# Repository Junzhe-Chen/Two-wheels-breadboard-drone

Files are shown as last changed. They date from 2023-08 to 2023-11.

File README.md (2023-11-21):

# Overview

The two wheel car is built onto a small breadboard, with an Arduino Uno attached at the bottom. There are two small DC motor which acts as the driver of the motor each with a dedicate full H bridge to control it. The robot also contains an ultrasonic sensor that is used to avoid obstacles. 

# Basic structure

The drone looks like this:

Overview of the drone

The drone is composed of 4 parts:

- 9V battery as the power source

9V battery power

- Arduino Uno R3 for the control

Arduino UNO

- Breadboard for attaching electrical components

Breadboard

- motors that makes the robot move

Motor

I tried to print out the wheel on a 3D printer, then I screwed up… **Bruh**

Failed 3D printing residue

If the wheel is designed to be 3D printed out, one thing to keep notice that is the wheel should have abundance contact with the plate of the 3D printer, which ensures the print stays in its place while printing. My first print has relatively thin structure (to save material) which does not provide enough contact area to the plate, causing the print to fail eventually. 

In my second design, I make the wheel more beefy and so far the print is going OK.

One of the objective of the project is to make the robot 

- able to move forward, backward, left and right
- can avoid obstacle (if there is a obstacle in the front of the robot, it should be able to go around and pass it)
- having the lighting in the front which can be turned on and off by the Arduino

## Movement control

### Little catch, Does the motor really work?

I have tested the motor with quite optimistic mindset for a bit, and found out it cannot drive the drone rather easily.

While the motor can perform well in empty load, it does not drive the wheel (which is around 20g of PLA print) that well. One reason is the small motor I used in this project is not designed to have great torque to drive heavy load. According to the datasheet shown below, it drives approximately 10g-cm torque, which is definitely a small value for driving the drone which have the total weight around 500g.

motor's datasheet

While if I can use a continuous servo motor, the torque it can provide is much more greater, which can potentially provide better drivability for this project. A typical SG90 microservo can provide around 2.5kg-cm torque, which is **much** bigger (250 times) than the motor that is mentioned previously. The datasheet for the SG90 servo motor is shown below;
microservo's datasheet

The microservo achieves that by applying gearbox inside the structure which by using small gear ratio, to increase the torque while reduce the speed. In this specific application, we don't need extremely fast spin of the motor (we are not making a fan or a propeller anyway), but we need generaous amount of torque to drive it forward. That is one reason why I decided to change the motor into microservo (which also saves plenty of breadboard space from the H bridge that is mentioned above).

### Working principle of the microservo

There are two types of microservo, one is those you can control the angle it turns between e.g. 0 and $180^\circ$, which is often used in the scenario where precision is the key. One good example of this type of microservo is [SG90](https://www.amazon.co.uk/s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)

However, in this project, the key is to make the wheel moving constantly. In this case, we should consider using a continuous microservo. The working mechanism of those servo motor is when you give a short pulse duration (for example, 0.5ms), it will rotate in one direction; When you apply a longer pulse (for example, 1.5ms), it will rotate in the opposite direction. This satisfies the bare minimum requirements for making a movement control for a two wheel drone, as it should be sufficient with forward and backward motion with controllable speed. A typical continuous servomotor is [FS90R](https://www.rapidonline.com/Feetech-FS90R-360-Continuous-Rotation-Micro-Servo-37-1335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)

in the Arduino library, we can include the servo header file, which provide the way to control most servo on the market. In my case, I am using the FS90R continuous microservo for my drone's movement. By using the header file, if I do `servo.write(90);` to my servo, it will stop and stay at neutral position. If I make the value smaller, it will constantly spin at one direction and same thing happen if I make the value bigger than 90, but the direction will be inverted. 

However, please take note that when we mount the motor to the breadboard, the two motor will be mirror to each other. Which means if both microservo have the same input (for example, `leftServo.write(80);` and `rightServo.write(80);` as the servo input), it will not go straight, but make the drone spin. In order to make the drone move forward, it should write the following:

```c++
void forward() {
  leftServo.write(90 - FORWARD_SPEED);
  rightServo.write(90 + FORWARD_SPEED);
}
```

But if I want the drone to spin around, I should write give the microservo the same input, like what is shown below:
```c++
void spin_left() {
  leftServo.write(90 - FORWARD_SPEED);
  rightServo.write(90 - FORWARD_SPEED);
}
```

## Choosing the battery

Interestingly, choosing the suitable battery for this project is the most time-consuming thing for me. The challenge in this part is to find a battery that can supply high current without too much voltage drop. The following picture shows that when the wheel is changing the direction, it will require high current up to around 0.8A to 1A. 

Current

One interesting thing is when the battery is drawing too much current, the battery voltage will decrease a lot. The unfortunate truth is if the supply voltage run below 4V for the Arduino, the Arduino will turn off, therefore the program will not run. 

Initially, I used the 1604S 9V battery as it marked “super heavy duty”, but it turned out not as that “heavy duty”. When driving the battery with 1A of current, the voltage quickly dropped down below 1V. After reviewing the [datasheet](https://www.farnell.com/datasheets/612533.pdf) for that battery, it shows that the main focus for the battery is longevity, as it will last quite a long time compare with other 9V battery. The battery that I chose for my project is 1604A (the golden one shown below) which has better current drivability and it is designed to handle high current. 

Batteries

As it said in the introduction page at [Farnell](https://uk.farnell.com/gp-batteries/gp1604-10/battery-alkaline-pp3-pk10/dp/5057050):

> High power, long-life alkaline PP3 batteries giving up to six times the life of ordinary zinc carbon batteries; ideal for high drain applications
> 

which turned out to be good enough for this project.

## Obstacle avoiding logic

In order to make the robot avoid obstacle, we need some sort of sensor that can be used to detect the distance between the robot and the surrounding. For this specific use case, the following sensor can be chosen:

- Ultrasonic sensor
    - Relatively cheap and easy-to-use, limited range (till around 0.5m), limited speed, take extra caution about the glitch when the sensor is too close to the wall
- IR sensor
    - Great accuracy and speed, limited range (depending to the ambient light) and light dependant, not that great for this use case
- LiDAR
    - [GreatScott!! video](https://youtu.be/_--8K1BW_O4)
    - adaptive scanning (sounds cool)

In this documentation, I will focus on the ultrasonic sensor one, because the sensor is readily available in my university lab and I had past experience with that. In the future, I might consider using LiDAR and according to GreatScott, it is definitely doable and it can give much more accurate control (just look at the commercial sweeping robot, they use LiDAR to avoid obstacle, meanwhile, map the room)

### Basics of ultrasonic sensor

As we all know, sound travels around $340m/s$ in the air. Remember this data, which will be quite useful in the future.

[insert image for better explanation]

 The principle of the ultrasonic sensor is to send a short pulse in certain time period, and receive the same pulse with the receiver. By calculating the time difference between sending and receiving signal, the distance can be calculated by the following equations:

$$
d=\frac{340}{2t}
$$

where $d$ represents the distance between the sensor and the obstacle, $t$ is the time between the pulse being sent and the time where signal being received.

By using this principle, we can write following codes in Arduino to sense the distance between the sensor and the obstacle.

```c++
void distance_measurement() {
    if (millis() > currentMillis + 100) {  // Distance measurement in every 100 milliseconds
      	currentMillis = millis();

	// generate 10-microsecond pulse to TRIG pin
      	digitalWrite(ULTRASONIC_TRIGGER_PIN, HIGH);
      	delayMicroseconds(10); 
      	digitalWrite(ULTRASONIC_TRIGGER_PIN, LOW);

      	// measure duration of pulse from ECHO pin
      	duration_us = pulseIn(ULTRASONIC_ECHO_PIN, HIGH);

      	// calculate the distance
      	distance_cm = 0.017 * duration_us; // Formular that is mentioned before
      	Serial.println("distance: ");
      	Serial.print(distance_cm);
      	// return distance_cm;
      	// print the value to Serial Monitor
    }
  }
```

According to my test, the ultrasonic sensor's readout is quite accurate. However, it does have some artifacts when the distance between the obstacle and the ultrasonic sensor is too close, which is why I put it around 2 or 3 centimeters inside of the drone to avoid the artifacts happens. The range of the ultrasonic sensor is from 2cm to 1 metre.
ultrasonic measurement

### Detailed look of obstacle avoidance logic with codes

To avoid the obstacle, we need to know few things:

- What is the threshold distance between the robot and the obstacle when you want the robot to avoid the obstacle?
- How does the robot determine whether it should turn left or turn right when facing an obstacle?

Which they sounds easy, but is actually a little tricky to implement when considering the limited space this design has.

As we all know for the ultrasonic sensor (which is the sensor chosen for this project), it only returns the distance in the front, but not the distance around the robot. In order to make the robot know the distance on the left and right side of the robot, there are the following few suggestions:

- Adding two more ultrasonic sensor, one on the left and another on the right. you will only have the gut of doing that if you have unlimited funds (Obviously, I am not), as well as plenty of space for the robot, which is not achievable on a small design like this.
- Mounting the ultrasonic sensor on a servo, making the sensor turn around to check the distance on the left and right hand side of the robot. It works quite like a sweeping radar, which can be quite interesting to make one one day. Unfortunately, there is not enough space for my project to implement this design.
- Rotating the robot to the left and the right to “peek” the distance. This solution is quite bad as it makes the robot constantly turning around. But due to the limited space for adding more components, this is the only way I can use.
- Surely there are more solutions other than that, maybe you can come up with better solution than me!

The flow chart for my version of obstacle avoidance logic is shown below:

Flow chart

where if the sensor returns the distance value less than the threshold, the robot will first move backward to avoid collision, then checking the left and right distance between the robot and the obstacle, so that it can find the easiest path for it to pass through.

Obstacle avoidance illustration

As for the left and right peek, the flow chart and the code is shown below:

flowchart int checkLeft

```cpp
int checkLeft() {
  STOP();
  delay(10);
  spin_left();
  delay(200);  // Calibrate this value till when doing one spin, the robot turns to 45 degrees
  distance_measurement();
  spin_right();
  delay(200); // Spin the robot back after checking left distance
  STOP();
  Serial.print(" >>> Distance to the left is: ");
  Serial.print(distance_cm);
  Serial.println("cm <<<");
  return distance_cm;
}
```

Same thing apply when checking the right side, the only difference will be that the `spin_left()` and `spin_right()` function will be inverted.

## Final demo

Here is a short video footage that shows how the obstacle avoidance function works

https://github.com/Junzhe-Chen/Two-wheels-breadboard-drone/assets/141964509/749089a3-922f-4cfe-97b0-32ad5c9f485c

The **circuit diagram** of the breadboard is shown below, I use [TinkerCAD](www.tinkercad.com) to create it.

![Breadboard diagram]
)

## Few notices and common mistakes

**Please check the following if your robot does not work, it might save you a day!**

1. The battery ground should share with the Arduino ground, if there are not sharing the same ground, the Arduino will be put in the floating state, therefore the voltage reference will not be accurate
2. Careful with your connection of the switch, the left and middle pin should connect to the positive Vin of the Arduino and the positive wire (red wire of the PP3) of the 9V battery. The negative input of the Arduino should not be connected to the switch. If the negative input is connected, when the switch is closed, it will **short** out the Arduino **which will make your unable to download, even worse, destroy your Arduino!**
3. When connecting the cable to the Arduino pin socket, make sure to make the sharp bend. This ensures good connection to the Arduino. You might encounter the robot behaves weirdly and ultrasonic sensor is constantly reading zero, this is usually caused by loose connection between Arduino and ultrasonic sensor
4. You may need to calibrate the microservo more or less. If the microservo does not stop given `servo.Write(90)`, spin the potentiometer at the back of the servo until its stops. Also, the speed of the left and right servo should be calibrated to the same, that makes the robot traveling straight when moving forward

## Bill of Materials:

The Bill of Materials (BoM) of this project is shown below:

If more knockoff brands are used, the cost should be within £40

I might consider making this into a kit in the future according to the requests.

| Component name | Component model  | Quantity | Price per unit | Price Total | Link  (Farnell) |
|---|---|---|---|---|---|
| Breadboard | | 1 | £2.60 | £2.60 | https://uk.farnell.com/multicomp/mcbb400/breadboard-solderless-300v-abs/dp/2395961 |
| Arduino | Arduino UNO R3 | 1 | £10 | £10.00 | Check price on ebay |
| Battery | 9V PP3 battery | 1 | £6 | £6.00 | https://uk.farnell.com/gp-batteries/gppva9vau073/battery-alkaline-pp3-9v/dp/3775309?st=9v%20batteries |
| Continuous servo  | FS90R | 2 | £9 | £18.00 | https://kitronik.co.uk/products/2589-fs90r-360-degree-continuous-rotation-servo |
| Ultrasonic sensor | | 1 | £3 | £3.00 | https://www.ebay.co.uk/itm/155434881025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 |
| Photoresistor | | 1 | | £0.00 | |
| Switch | Any spare switch | 1 | | £0.00 | |
| | | | Subtotal: | £39.60 |

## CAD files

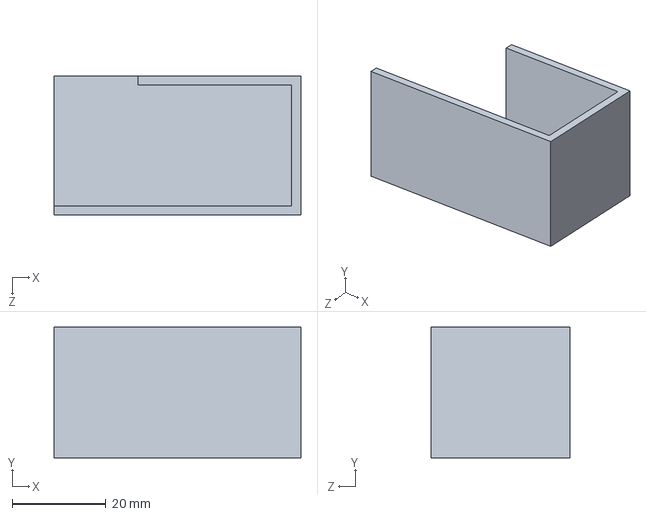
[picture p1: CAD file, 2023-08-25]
3D model, SLDPRT files/Battery holder.SLDPRT
52.8 x 28.0 x 29.8 mm

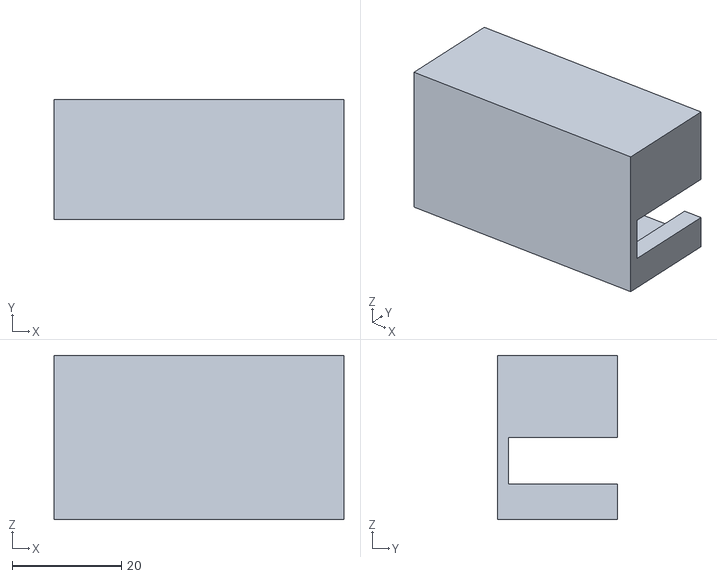
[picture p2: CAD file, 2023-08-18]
Breadboard drone 3D files/Battery holder V1.1.STL
53.0 x 22.0 x 30.0

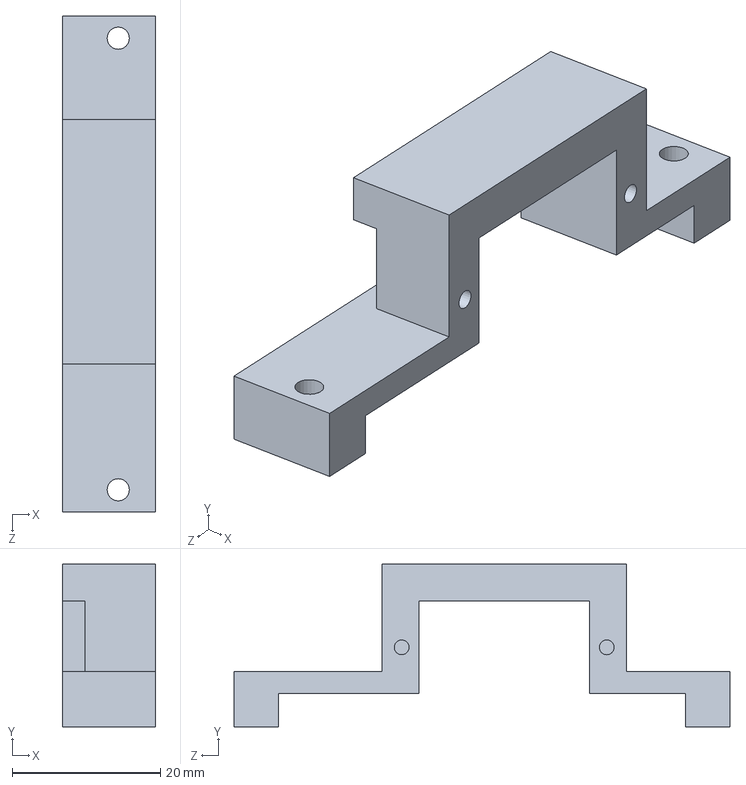
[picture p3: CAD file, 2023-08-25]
3D model, SLDPRT files/Right servo lock.SLDPRT
12.5 x 22.0 x 67.0 mm

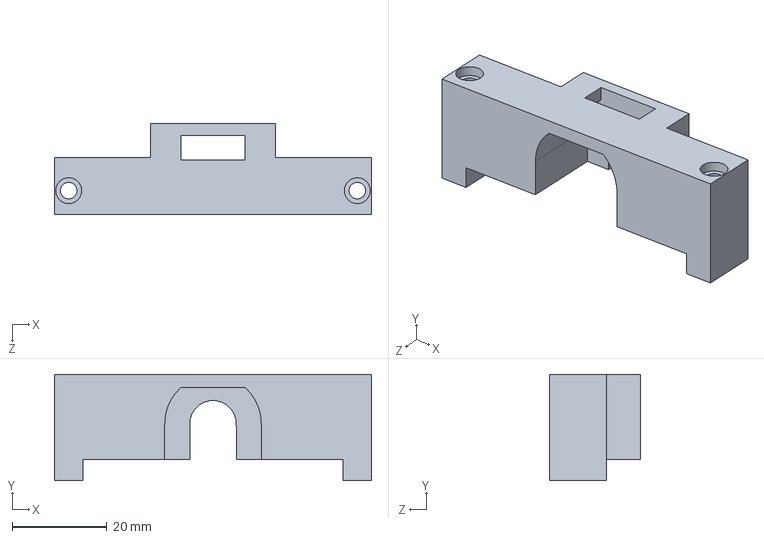
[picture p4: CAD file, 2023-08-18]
Breadboard drone 3D files/DC motor lock V2.3 straight sink.SLDPRT
67.0 x 22.5 x 19.1 mm

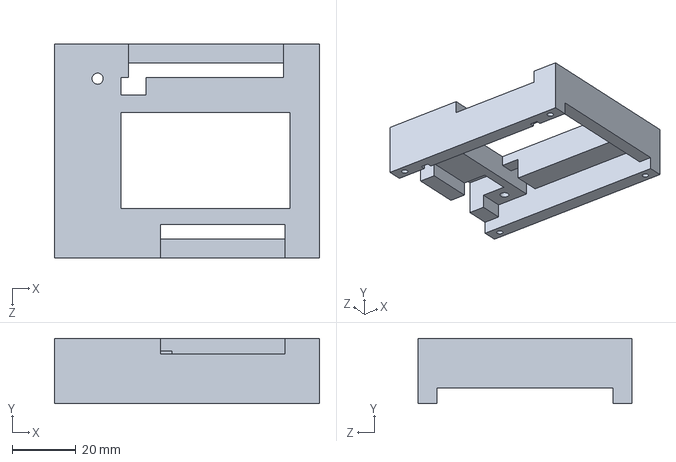
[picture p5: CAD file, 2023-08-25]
3D model, SLDPRT files/Arduino cover.SLDPRT
83.0 x 20.5 x 67.0 mm

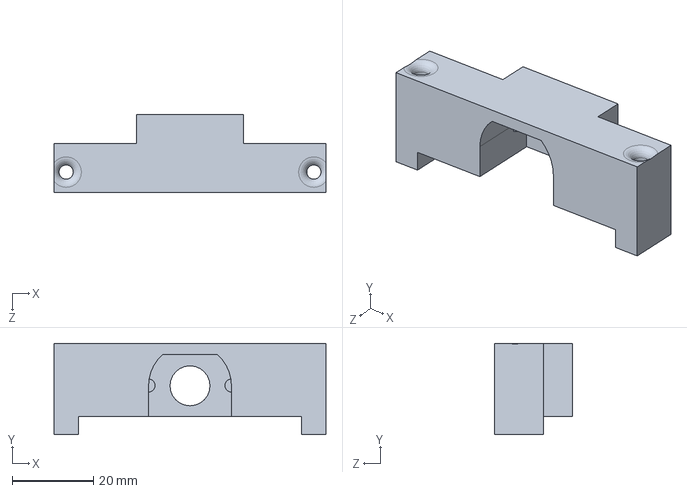
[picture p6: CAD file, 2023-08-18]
Breadboard drone 3D files/DC motor lock V2.2.SLDPRT
67.0 x 22.5 x 19.1 mm

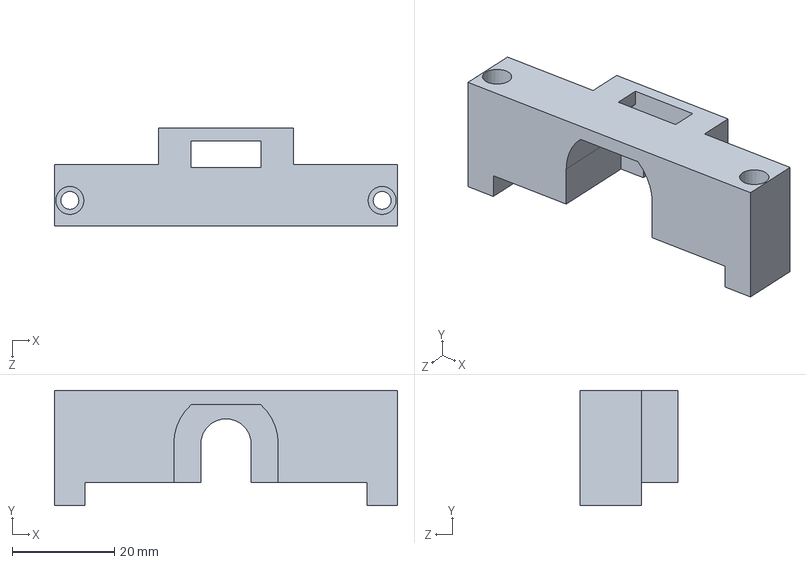
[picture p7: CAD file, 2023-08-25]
3D model, SLDPRT files/DC motor lock.SLDPRT
67.0 x 22.5 x 19.1 mm

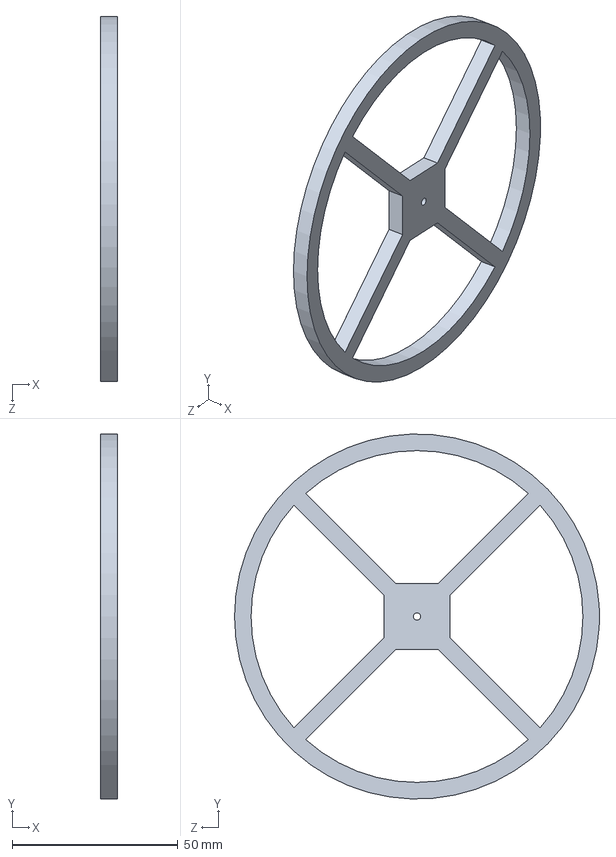
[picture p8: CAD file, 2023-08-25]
3D model, SLDPRT files/Wheel with Servo Cross mount.SLDPRT
5.00 x 110.0 x 110.0 mm

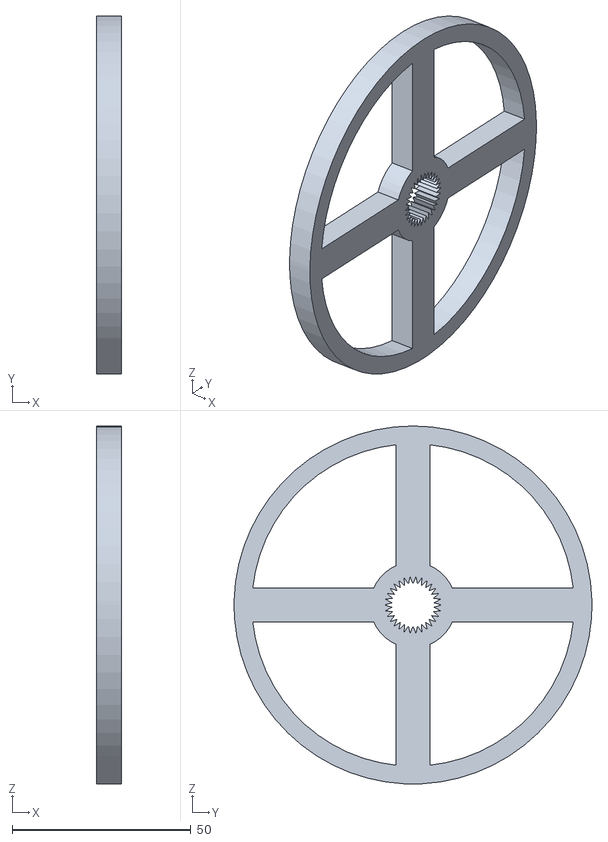
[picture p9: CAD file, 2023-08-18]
Breadboard drone 3D files/Wheel V1.2 test.STL
7.00 x 100.0 x 100.0

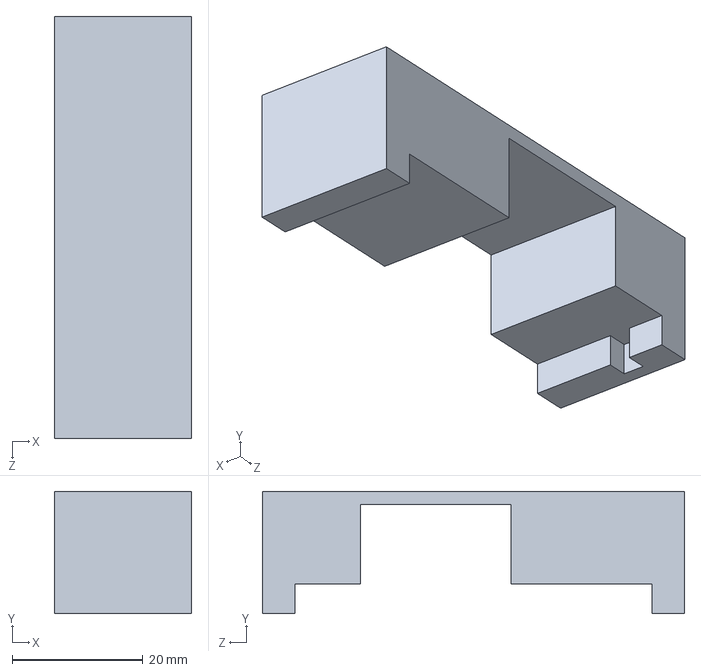
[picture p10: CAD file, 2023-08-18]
Breadboard drone 3D files/Servo lock V1.1.SLDPRT
21.0 x 18.7 x 64.5 mm

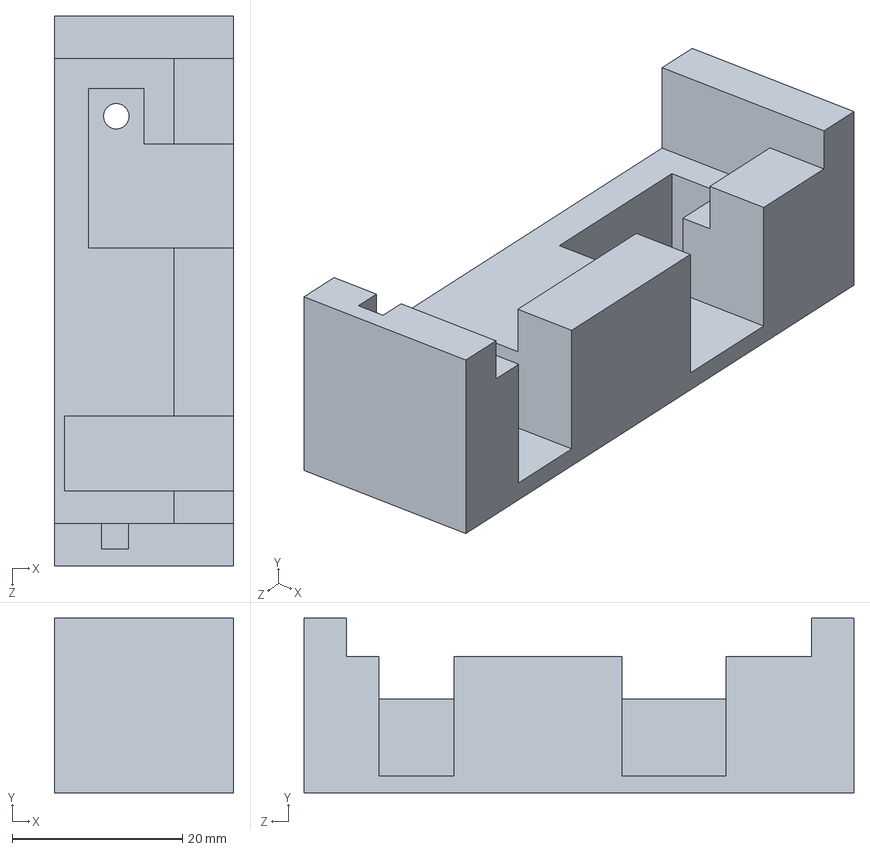
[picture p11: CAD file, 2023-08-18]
Breadboard drone 3D files/Robot base cover V1.2.SLDPRT
21.0 x 20.5 x 64.5 mm

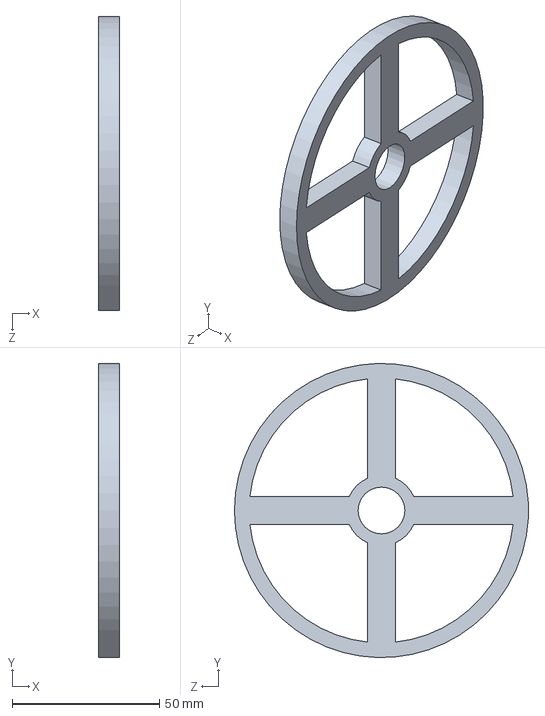
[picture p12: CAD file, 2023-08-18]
Breadboard drone 3D files/Wheel V1.2 no tooth test.SLDPRT
7.00 x 100.0 x 100.0 mm

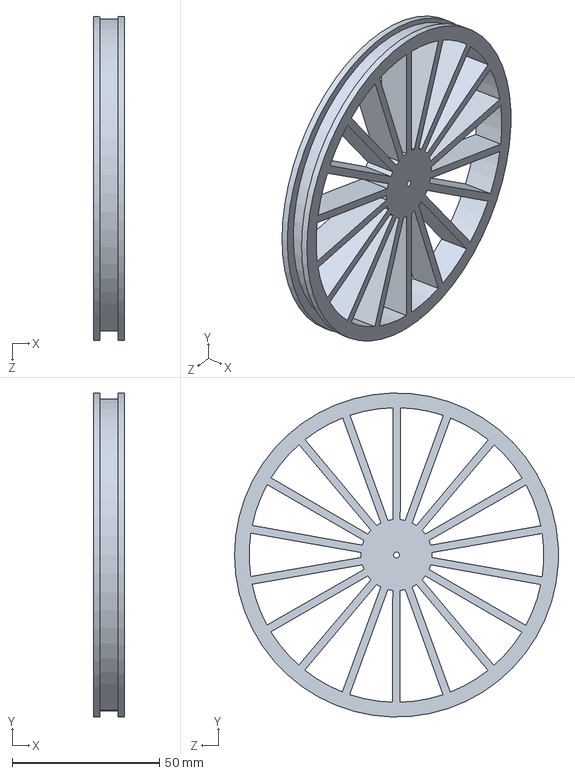
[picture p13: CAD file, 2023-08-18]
Breadboard drone 3D files/Wheel V1.3.SLDPRT
10.5 x 110.0 x 110.0 mm

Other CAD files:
3D model, SLDPRT files/Left servo lock.SLDPRT
Breadboard drone 3D files/Arduino cover.SLDPRT
Breadboard drone 3D files/DC motor lock V2.3.1 straight sink.STL
Breadboard drone 3D files/Arduino cover V1.3.STL
Breadboard drone 3D files/Battery holder.SLDPRT
Breadboard drone 3D files/Arduino cover V1.2.STL
Breadboard drone 3D files/Arduino cover.STL
Breadboard drone 3D files/DC motor lock V2.1.SLDPRT
Breadboard drone 3D files/DC motor lock V2.1.STL
Breadboard drone 3D files/DC motor lock V2.2 straight sink.SLDPRT
Breadboard drone 3D files/DC motor lock V2.2 straight sink.STL
Breadboard drone 3D files/DC motor lock V2.2.STL
Breadboard drone 3D files/DC motor lock V2.3 straight sink.STL
Breadboard drone 3D files/Printing file/Robot base cover V1.2.STL
Breadboard drone 3D files/Printing file/Servo lock V1.1.STL
Breadboard drone 3D files/Robot base cover.STL
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

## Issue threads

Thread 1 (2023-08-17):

Picture library

Junzhe-Chen, 2023-08-17:
Please upload your picture here

Junzhe-Chen, 2023-08-17:
Circuit diagram about the working mechanism of H bridge

H bridge driver
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

H bridge, M1 and M4 conducting
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

H bridge, M2 and M3 conducting
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

H bridge, STOP
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

Junzhe-Chen, 2023-08-17:
Building blocks of the drone:

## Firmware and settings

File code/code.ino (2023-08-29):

// Libraries
// **************************************************************************************************
#include <Servo.h>
Servo leftServo, rightServo;
// **************************************************************************************************
// Constants
const int ULTRASONIC_TRIGGER_PIN = 7;
const int ULTRASONIC_ECHO_PIN = 8;
const int LEFT_SERVO_PIN = 5;
const int LEFT_SIGNAL_LIGHT = 6;
const int RIGHT_SERVO_PIN = 10;
const int RIGHT_SIGNAL_LIGHT = 9;
const int FRONT_LED = 11;
const int LIGHT_SENSOR_PIN = A5;
// Variables
float duration_us, distance_cm;
int light_intensity;
int leftServoSpeed, rightServoSpeed = 90;
// According to the datasheet, when inputting 90 the servo should stop. If the servo does not stop
// at 90, try to calibrate the potentiometer until the servo stop
unsigned long startMillis;
unsigned long currentMillis;
// **************************************************************************************************
// User determined values
const int FORWARD_SPEED = 10;            // Set the value between 0 and 90
const int BACKWARD_SPEED = 10;           // Set the value between 0 and 90
const int DISTANCE_LOWER_BOUNDARY = 15;  // Set the lower boundary between the drone and the obstacle
const int DISTANCE_UPPER_BOUNDARY = 20;  // Set the upper boundary between the drone and the obstacle
const int OFFSET_ANGLE = 200;


void setup() {
  // This part is for setting up the Arduino pins and serial connection, please keep it unchanged
  pinMode(ULTRASONIC_TRIGGER_PIN, OUTPUT);
  pinMode(ULTRASONIC_ECHO_PIN, INPUT);
  pinMode(LEFT_SIGNAL_LIGHT, OUTPUT);
  pinMode(RIGHT_SIGNAL_LIGHT, OUTPUT);
  pinMode(LIGHT_SENSOR_PIN, INPUT);
  pinMode(FRONT_LED, OUTPUT);
  leftServo.attach(5);
  rightServo.attach(10);
  Serial.begin(9600);
  startMillis = millis();
}

// ******************************************************************************************************
void loop() {

  obstacle_avoidance_logic();
  light_sensing();
  // forward();
}
// ******************************************************************************************************




// Functions for the movement (servo)
// ******************************************************************************************************
void forward() {
  // leftServo.write(90 - FORWARD_SPEED);
  // rightServo.write(90 + FORWARD_SPEED);
  leftServo.write(83);
  rightServo.write(100);
  digitalWrite(LEFT_SIGNAL_LIGHT, LOW);
  digitalWrite(RIGHT_SIGNAL_LIGHT, LOW);
}

void backward() {
  // leftServo.write(90 + FORWARD_SPEED);
  // rightServo.write(90 - FORWARD_SPEED);
  leftServo.write(100);
  rightServo.write(83);
  digitalWrite(LEFT_SIGNAL_LIGHT, HIGH);
  digitalWrite(RIGHT_SIGNAL_LIGHT, HIGH);
}

void spin_left() {
  leftServo.write(90 - FORWARD_SPEED);
  rightServo.write(90 - FORWARD_SPEED);
  digitalWrite(LEFT_SIGNAL_LIGHT, HIGH);
  digitalWrite(RIGHT_SIGNAL_LIGHT, LOW);
}

void spin_right() {
  leftServo.write(90 + FORWARD_SPEED);
  rightServo.write(90 + FORWARD_SPEED);
  digitalWrite(LEFT_SIGNAL_LIGHT, LOW);
  digitalWrite(RIGHT_SIGNAL_LIGHT, HIGH);
}

void STOP() {
  leftServo.write(90);
  rightServo.write(90);
  digitalWrite(LEFT_SIGNAL_LIGHT, HIGH);
  digitalWrite(RIGHT_SIGNAL_LIGHT, HIGH);
}




// ******************************************************************************************************
void distance_measurement() {
  if (millis() > currentMillis + 10) {  // Distance measurement in every 100 milliseconds
    currentMillis = millis();
    // generate 10-microsecond pulse to TRIG pin
    digitalWrite(ULTRASONIC_TRIGGER_PIN, HIGH);
    delayMicroseconds(10);
    digitalWrite(ULTRASONIC_TRIGGER_PIN, LOW);

    // measure duration of pulse from ECHO pin
    duration_us = pulseIn(ULTRASONIC_ECHO_PIN, HIGH);

    // calculate the distance
    distance_cm = 0.017 * duration_us;

    // print the value to Serial Monitor
    Serial.print("distance: ");
    Serial.print(distance_cm);
    Serial.println(" cm");
  }
}

int checkLeft() {
  STOP();
  delay(10);
  spin_left();
  delay(200);  // Calibrate this value till when doing one spin, the robot turns to 45 degrees
  distance_measurement();
  spin_right();
  delay(200);  // Spin the robot back after checking left distance
  STOP();
  Serial.print(" >>> Distance to the left is: ");
  Serial.print(distance_cm);
  Serial.println("cm <<<");
  return distance_cm;
}

int checkRight() {
  STOP();
  delay(10);
  spin_right();
  delay(200);  // Calibrate this value till when doing one spin, the robot turns to 45 degrees
  STOP();
  distance_measurement();
  Serial.print(" >>> Distance to the right is: ");
  Serial.print(distance_cm);
  Serial.println("cm <<<");
  return distance_cm;
}

// ******************************************************************************************************
void obstacle_avoidance_logic() {
  int distanceLeft, distanceRight;
  distance_measurement();
  if (distance_cm <= DISTANCE_LOWER_BOUNDARY) {

    backward();  // When the distance is lower than the threshold, going back
    delay(200);

    // Measure the left and right distance between the drone and the obstacle, go through the side with lower distance
    checkLeft();
    checkRight();
    distanceLeft = checkLeft();
    distanceRight = checkRight();
    STOP();
    delay(200);

    if (distanceLeft <= distanceRight) {
      // When left distance is less than right distance, that means there is a gap at left, turn left and go straight
      spin_right();
      delay(OFFSET_ANGLE);
      STOP();
      delay(100);
      forward();
    } else {
      // When left distance is more than right distance, that means there is a gap at right, turn right and go straight
      spin_left();
      delay(OFFSET_ANGLE);
      STOP();
      delay(100);
      forward();
    }
  } else {
    forward();  // When the distance is higher than the threshold, going forward
  }
  delay(100);
}

// ******************************************************************************************************
void light_sensing() {
  Serial.println("light sensing debug");
  if (millis() > currentMillis + 100) {
    currentMillis = millis();
    light_intensity = analogRead(LIGHT_SENSOR_PIN);
    Serial.println(light_intensity);
    if (light_intensity < 250) {
      digitalWrite(FRONT_LED, HIGH);
      Serial.println("Turn on the front light");
    } else {
      digitalWrite(FRONT_LED, LOW);
    }
  }
}

//// Functions that controls the movement of the robot drone
//// ******************************************************************************************************
void distance_maintaining_logic() {
  if (distance_cm < 8) {
    backward();
    Serial.println(">>>Going back");
  } else if (distance_cm > 12) {
    forward();
    Serial.println(">>>Going forward");
  } else {
    STOP();
  }
}

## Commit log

2023-08-18 Adding quote for flyback diode, highlight code block
2023-08-18 Add 3D models
    [Arduino cover V1.2.STL, Arduino cover V1.3.STL, Arduino cover.SLDPRT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]
2023-08-18 Unfortunately, my ultrasonic sensor only has the range of half a meter...
2023-08-19 Fixing the code + add distance maintain function
    [code.ino]
2023-08-21 Oops!, I don't want to use the motor anymore, here is why
2023-08-21 Update ultrasonic reading
2023-08-22 Adding avoidance logic V1.1
    [code.ino]
2023-08-24 Adding a flowchart for the checkLeft function
2023-08-25 Adding "choosing the battery" chapter
2023-08-29 Fixing the conflict between the lighting and obstacle avoidance
    [code.ino]
2023-09-05 Adding TinkerCAD circuit diagram
2023-09-12 Adding BoM
